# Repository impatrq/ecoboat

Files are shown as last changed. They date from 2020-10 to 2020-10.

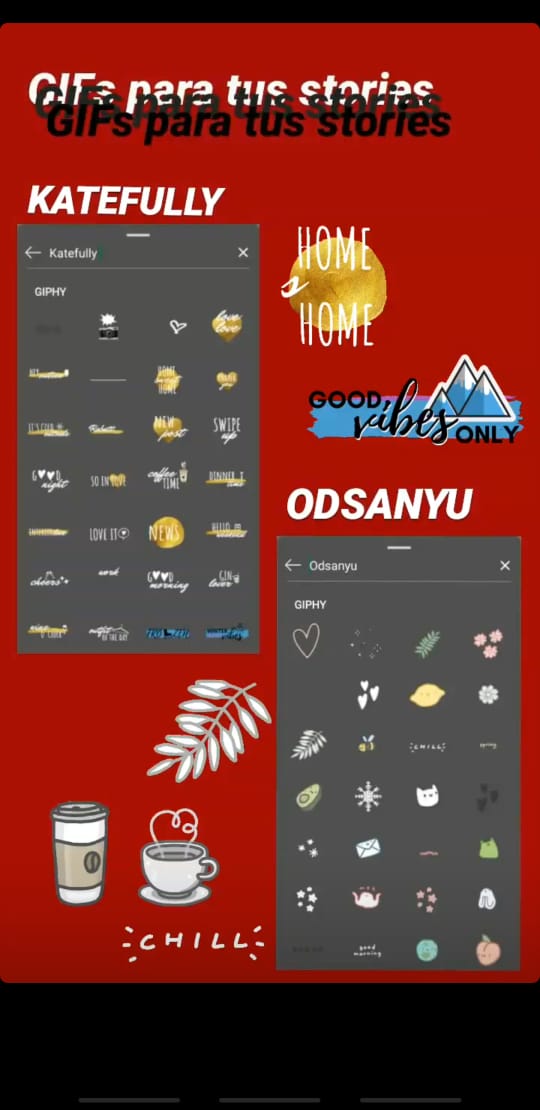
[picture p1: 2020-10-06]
Diseño/Instagram/WhatsApp Image 2020-04-10 at 20.14.38 (1).jpeg

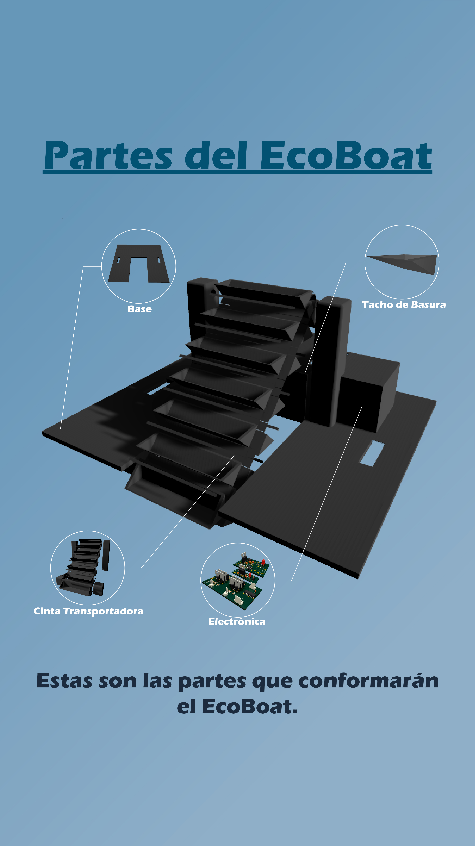
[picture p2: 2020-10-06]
Diseño/Instagram/Partes Historias-05.jpg

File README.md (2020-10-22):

# EcoBoat
Bienvenidos al repositorio de EcoBoat.

## Software

En la carpeta de "Software" se encontrarán con varios archivos:

- EcoBoat1.0: Es el código principal, donde se ejecuta el funcionamiento del barco y todas las librerías utilizadas para dicho fin.
- Motores: Es la librería (desarrollada por el equipo de EcoBoat) que se utiliza para controlar los motores.
- SensoresUS: Es la librería (desarrollada por el equipo de EcoBoat) que utilizamos para realizar las mediciones con los sensores Ultrasónicos.
- RedNeuronal: Es la librería (desarrollada por el equipo de EcoBoat) que contiene el código de la Red Neuronal y su entrenamiento.
- Módulo_Master: Es el programa utilizado para recibir la información y transferirla mediante sockets a la Interfaz de Usuario.
- Interfaz de Usuario: En esta carpeta se encuentran los códigos de la interfaz de usuario.
- Simulación: En esta carpeta encontrarán todo lo relacionado al entrenamiento de la Red Neuronal.
  - Aplicación Ejecutable: Aquí se encuentra la aplicación de la cual se obtienen los datos de entrenamiento para la red, es decir, la red aprende de las acciones realizadas en dicha aplicación.
  - Código fuente: Contiene el programa de la simulación.
  - trainData: En esta carpeta se guardan los archivos con la información de entrenamiento.

## Hardware

En esta carpeta se encuentran los diseños de todas las placas utilizadas:

- Circuito de Control de Marcha: Circuito utilizado para controlar los 3 motores del EcoBoat
- Fuente de 12V a 5V: regulador de tensión de 12 a 5V.
- Regulador de Carga: Es el circuito que controla la carga de la batería utilizando un panel solar.
- SensoresUS: Esta placa cumple la función de sincronizar la toma de datos de los sensores Ultrasónicos.
- Diagrama de Interconexión de circuitos: Es un diagrama que muestra como se conectan todas las placas del proyecto.

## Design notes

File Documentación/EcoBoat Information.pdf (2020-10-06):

Introduction:
EcoBoat is a school project whose objectives are to combat contamination by using a self-driving boat that collects floating residues from rivers and also to encourage people to take steps to prevent pollution.
Now we are working on a reduced-scale prototype. However, once this prototype is working, we intend to build this boat on a larger scale so that it can be used in rivers all around the world.

General Description:
EcoBoat will be at a charging station where it will charge by using solar energy, which will reduce contamination and will not generate any kind of residues. The station will be equipped with barriers to prevent the boat from being driven by the river's current.
Once the batteries are fully charged, the ship will set sail. This project will be provided with an autopilot which will controls every system of the EcoBoat; this way, there will be no need of a human to operate it. However, there will be a server which will have all the information needed to check whether the boat is working properly or not.
The user would have to introduce a route for the autopilot to follow. Once the boat is moving, it will catch the floating residues with the help of pitchers mounted in a conveyor belt and it will store them in a trash deposit in the back of the vehicle. When the route has all been covered, a person shall remove the deposit from the ship. It will go back to the charging station by its own means.

Technical Description:
EcoBoat will make use of a solar panel to charge its batteries. The user should establish a route for the boat to clean. This project will have a GPS in order to determine its location and a series of waypoints (in coordinates) will be established by an algorithm depending on the route previously introduced. This way, boat program will action its engine and its rudder in order to move it in the right direction. It will also be provided with ultrasonic sensors to prevent the ship from crashing with the borders of the river. Furthermore, it will have sounding lines to determine if the water level is enough to sail and to detect if there are any other ships nearby (in which case the boat will just stop).
Using pitchers, the boat will pick up the floating residues from the water and put them into a deposit. When EcoBoat finalizes its route, the trash will be removed manually and it will go back to the charging station.
This project will also have a real time diagnosis system of every part of the boat. This will be displayed in a comfortable graphic interface from a remote station.

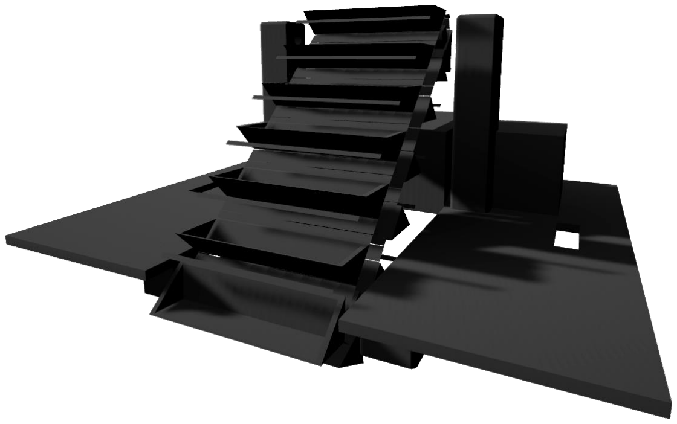
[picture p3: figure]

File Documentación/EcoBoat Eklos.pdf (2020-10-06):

# EcoBoat

Este proyecto consiste en un vehículo acuático diseñado para recolectar los desechos flotantes de ríos. Nuestro objetivo es reducir la contaminación de las aguas y concientizar sobre la contaminación causada por los residuos.

Actualmente estamos trabajando en un prototipo de tamaño reducido. No obstante, nuestro objetivo es que una vez que este sea funcional, podamos producir, este proyecto, en una escala más grande para poder recolectar mayor cantidad de basura. Este sistema podría ser utilizado por el Estado para mantener limpios todos los ríos de Argentina

Gracias a nuestro sistema de extracción de los elementos que se encuentran en la superficie de los ríos, podríamos no solo limpiar la superficie, sino también disminuir en gran medida la cantidad de basura que -de no ser extraída- empezaría a acumularse en el fondo del agua o llegaría al mar y el océano.

Además del gran impacto que este proyecto generaría en el medio ambiente, también buscamos concientizar a las personas sobre los residuos que arrojan al agua. Si trabajamos todos juntos, podemos reducir la contaminación de forma drástica

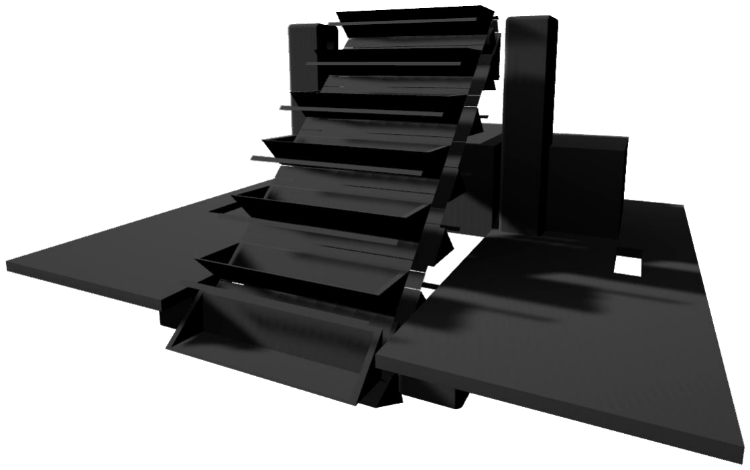
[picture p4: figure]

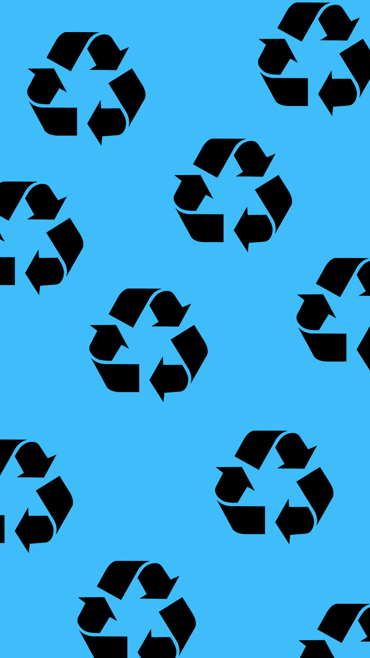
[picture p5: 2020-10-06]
Diseño/Instagram/Historias Trivia/reciclar.png

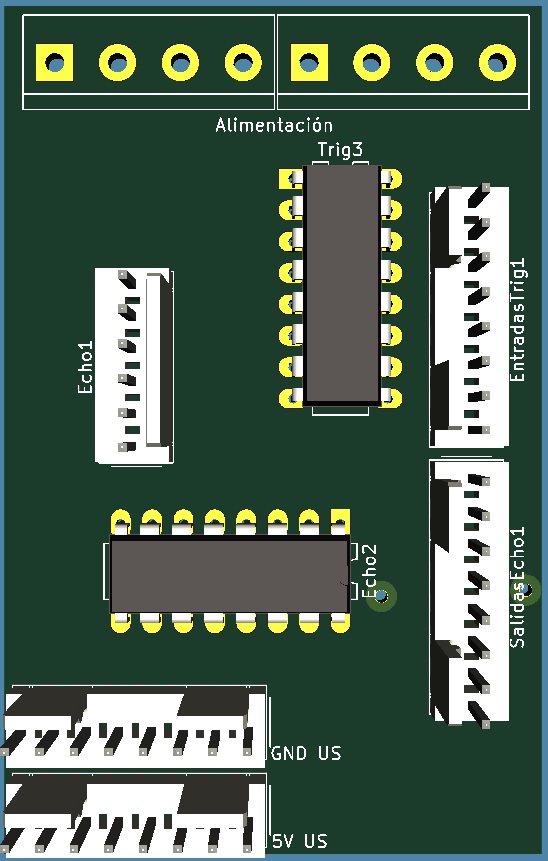
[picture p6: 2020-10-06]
Hardware/SensoresUS/3D SensoresUS.jpg

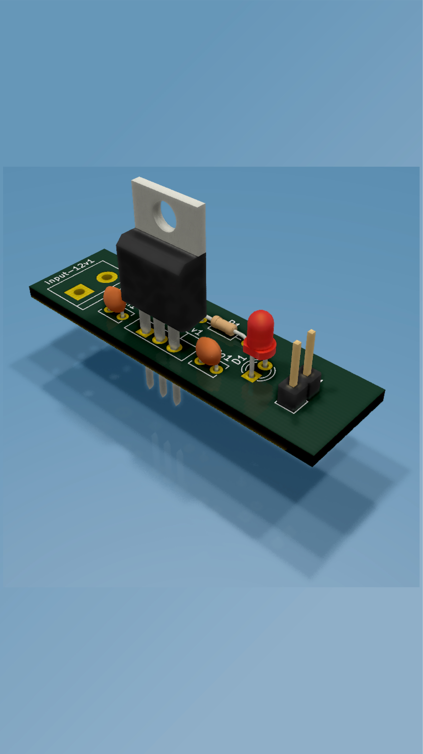
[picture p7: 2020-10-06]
Diseño/Instagram/Historia Circuito Regulador De Tensión-06-06-06.jpg

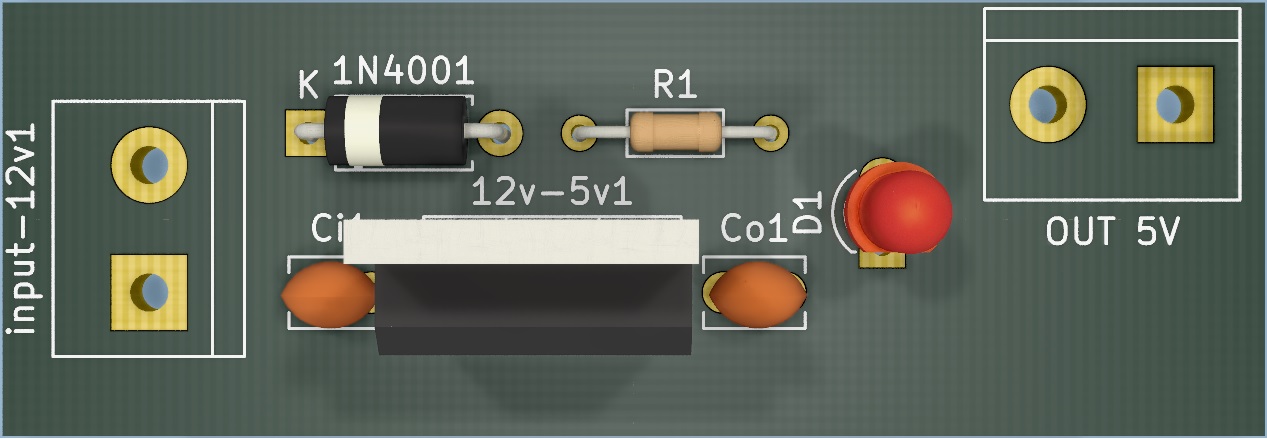
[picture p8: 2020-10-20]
Hardware/fuente 12v a 5v/Fuente 12V a 5V 3D.jpg

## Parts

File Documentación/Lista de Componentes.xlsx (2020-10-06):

Componente | Cantidad
Placa de Cobre 20x15 | 1
Cloruro Férrico | 1
FLUX aerosol | 1
Molex Macho 2 Pines | 2
Molex Hemra 2 Pines | 2
Molex Macho 3 Pines | 1
Molex Hembra 3 Pines | 1
Molex Macho 4 Pines | 2
Molex Hembra 4 Pines | 2
Molex Macho 6 Pines | 1 | Estos conectores no tienen que ser necesariamente molex
Molex Hembra 6 Pines | 1 | puede ser cualquier conector con 2,54mm de distancia entre
Molex Macho 7 Pines | 1 | pines y que tenga macho y hembra (con sus respectivos
Molex Hembra 7 Pines | 1 | conectores para cables)
Molex Macho 8 Pines | 4
Molex Hembra 8 Pines | 4
Conectores para Molex | 80 | (Terminales utilizados para conectar un cable a un molex hembra)
Pines Hembra a Macho | 40 | Tira de pines (2,54mm de separación entre pines) son para conectar a una raspberry
Termocontraible ø5mm | 80cm
Bornera 2 Polos | 11 | 126VP- 2P
Bornera 3 Polos | 2 | 126VP- 3P
MOSFET IRF9530 | 3
MOSFET IRF640 | 4
4N25 | 8
Resistencia 1,2K | 1
Resistencia 82K | 1
Preset 200K | 1 | Multivuelta
Preset 500K | 1 | Multivuelta
Diodo Zener 15V 1W | 1
Fusible 10A | 1
Capacitor 330nF | 3
Capacitor 100nF | 3
LM7805 | 2
LS157 | 1
MCP3008 | 1 | Conversor Analógico Digital con soporte para SPI
74HC237 | 1 | 3to8 dec
74LS151 | 1 | 8to1 mux
ACS712 ±20A | 2 | Sensor de Efecto HALL
Módulo RF NRF24 | 2 | Módulo de radio frecuencia

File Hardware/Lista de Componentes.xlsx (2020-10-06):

Componente | Cantidad
Placa de Cobre 20x15 | 1
Cloruro Férrico | 1
Molex Macho 2 Pines | 2
Molex Hemra 2 Pines | 2
Molex Macho 3 Pines | 1
Molex Hembra 3 Pines | 1
Molex Macho 4 Pines | 2
Molex Hembra 4 Pines | 2
Molex Macho 6 Pines | 1
Molex Hembra 6 Pines | 1
Molex Macho 7 Pines | 1
Molex Hembra 7 Pines | 1
Molex Macho 8 Pines | 4
Molex Hembra 8 Pines | 4
Conectores para Molex | 80 | (Terminales utilizados para conectar un cable a un molex hembra)
Pines Hembra a Macho | 40
Termocontraible | 80cm
Bornera 2 Pines | 8
Bornera 5 Pines | 1
Bornera 4 Pines | 2
MOSFET IRF9530 | 5
MOSFET IRF640 | 5
Transistores BJT | 8
Resistencia 220 | 8
Resistencia 1K | 1
Resistencia 1,2K | 1
Resistencia 10K | 8
Resistencia 82K | 1
Resistencia 270K | 1
Preset 200K | 1
Preset 500K | 1
Diodo | 1
Diodo Zener 15V | 1
Diodo LED | 2
Fusible 10A | 1
Capacitor 330nF | 3
Capacitor 100nF | 3
LM7805 | 2
Operacional | 1
UNL2003 | 1
MCP3008 | 1
74HC237 | 1
74LS151 | 1
ACS712 ±20A | 2
Módulo RF NRF24 | 2
Batería ciclo profundo | 1
Panel Solar | 1

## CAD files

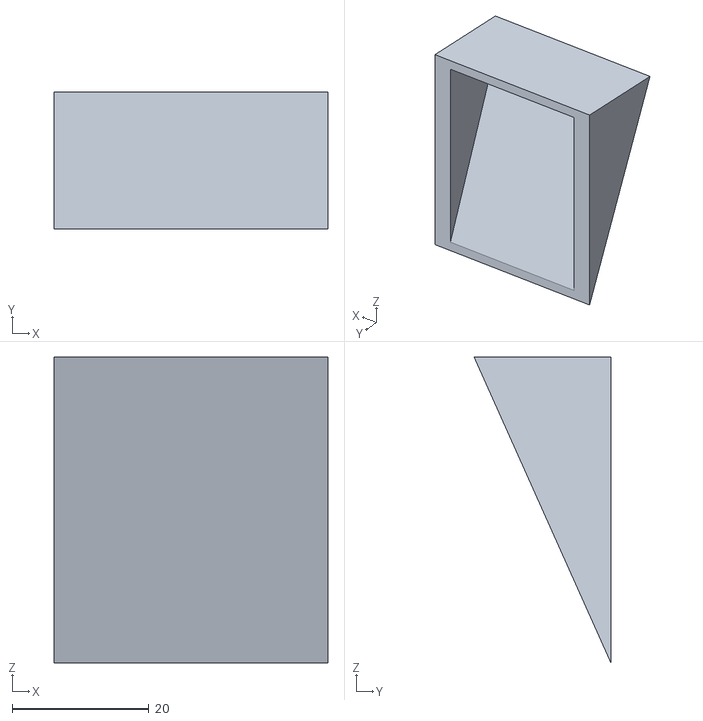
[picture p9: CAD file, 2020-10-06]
Estructura/Modelos 3D/Depósito de Basura.obj
40.0 x 20.0 x 44.7

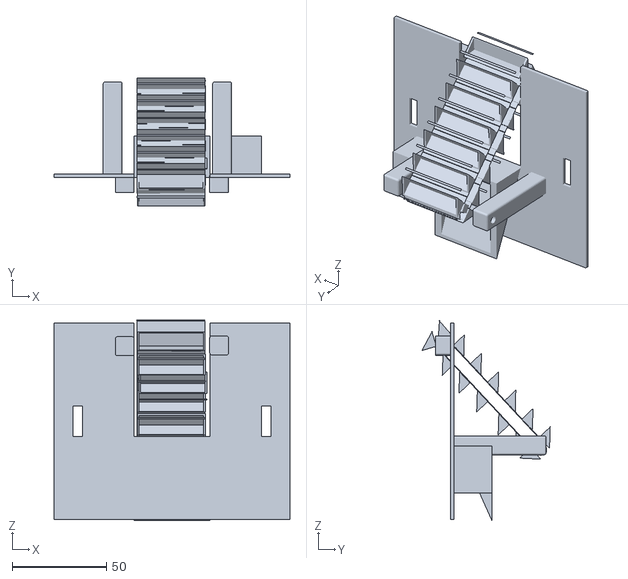
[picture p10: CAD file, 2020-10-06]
Estructura/Modelos 3D/diseño final.obj
125.0 x 68.0 x 106.2

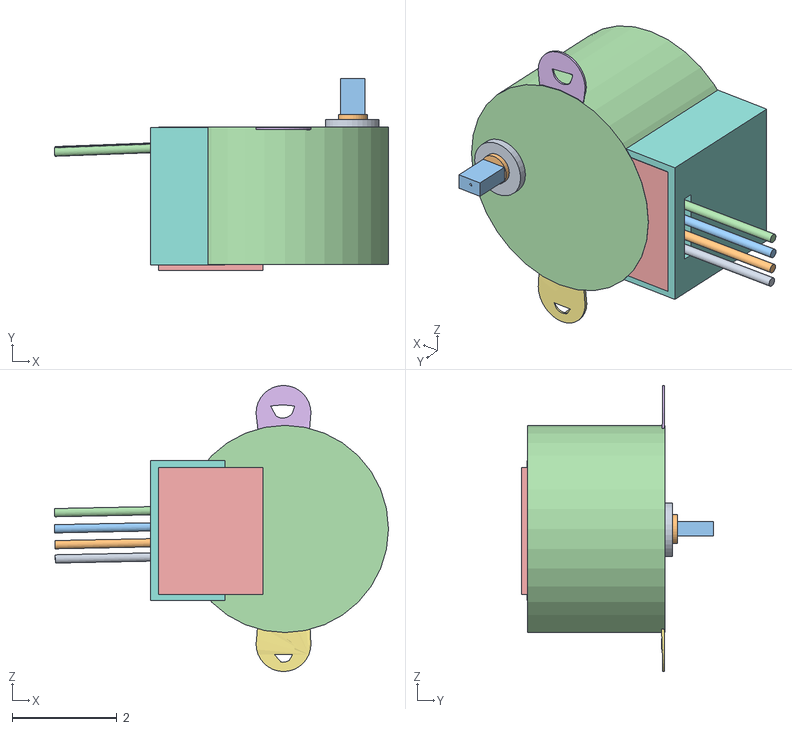
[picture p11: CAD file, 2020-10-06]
Estructura/Modelos 3D/Motor Paso a Paso.obj
6.39 x 3.68 x 5.47
Plane.025_Plane.006
Cylinder_Cylinder.003
Plane.026_Plane.007
Cylinder.003_Cylinder.004
Cylinder.004_Cylinder.005
Cube_Cube.001
Cylinder.005_Cylinder

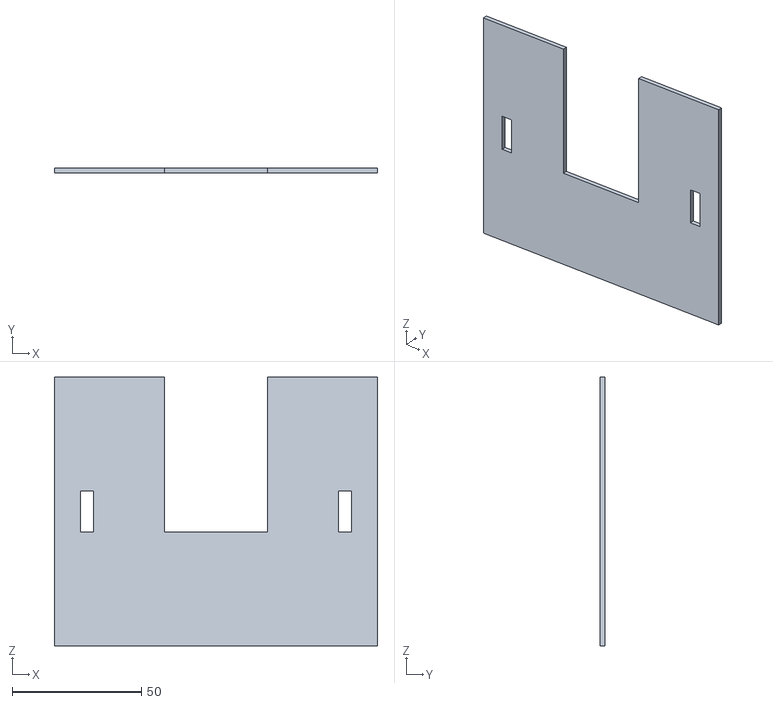
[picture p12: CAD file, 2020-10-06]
Estructura/Modelos 3D/Base.obj
125.0 x 2.00 x 104.1

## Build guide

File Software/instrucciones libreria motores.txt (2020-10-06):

paso a paso:

crear un objeto de la clase PaP con los 4 pines a usar como parametro: (pin1, pin2, pin3, pin4)
para girar en sentido horario usar la funcion girarH(grados)
para girar en sentido anti horario usar la funcion girarAH(grados)

motores lineales:

crear un objeto de la clase puenteH con los dos pines como parametro
el primer pin gira hacia la derecha y el segundo a la izquierda
funciones: para girar hacia la derecha: girarD()
	   para girar hacia la izquierda: girarI()
	   para frenar: detener()

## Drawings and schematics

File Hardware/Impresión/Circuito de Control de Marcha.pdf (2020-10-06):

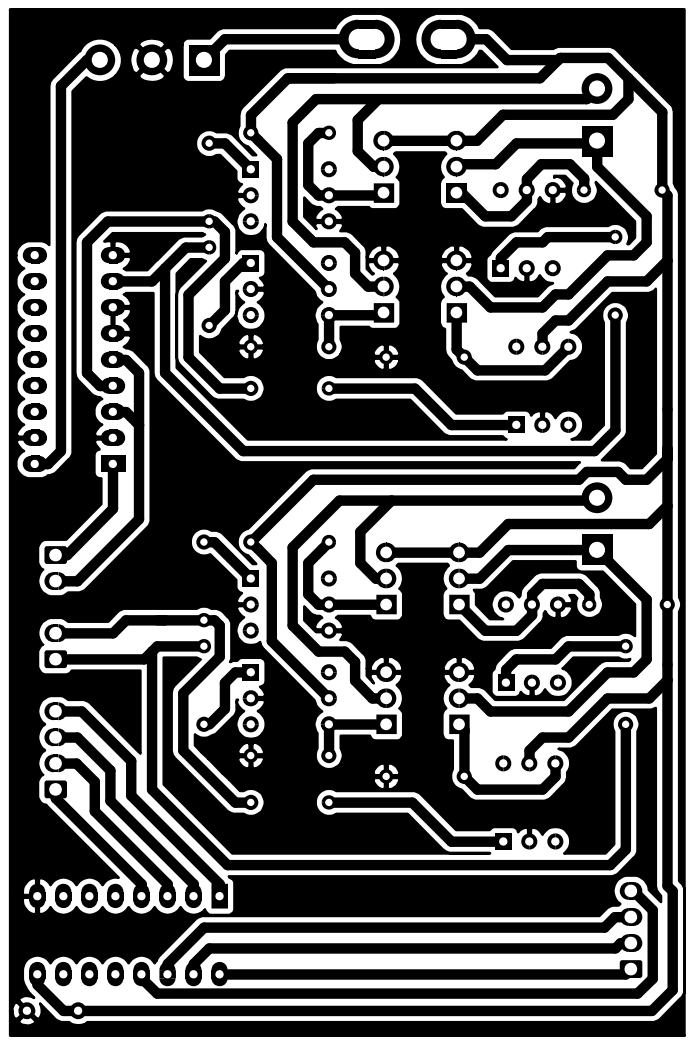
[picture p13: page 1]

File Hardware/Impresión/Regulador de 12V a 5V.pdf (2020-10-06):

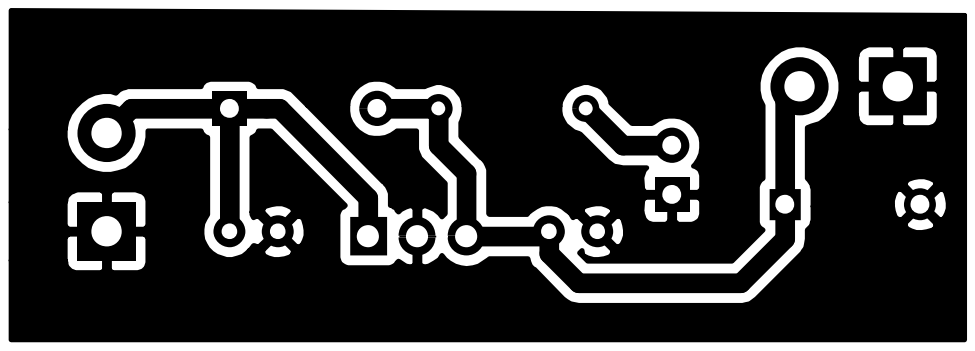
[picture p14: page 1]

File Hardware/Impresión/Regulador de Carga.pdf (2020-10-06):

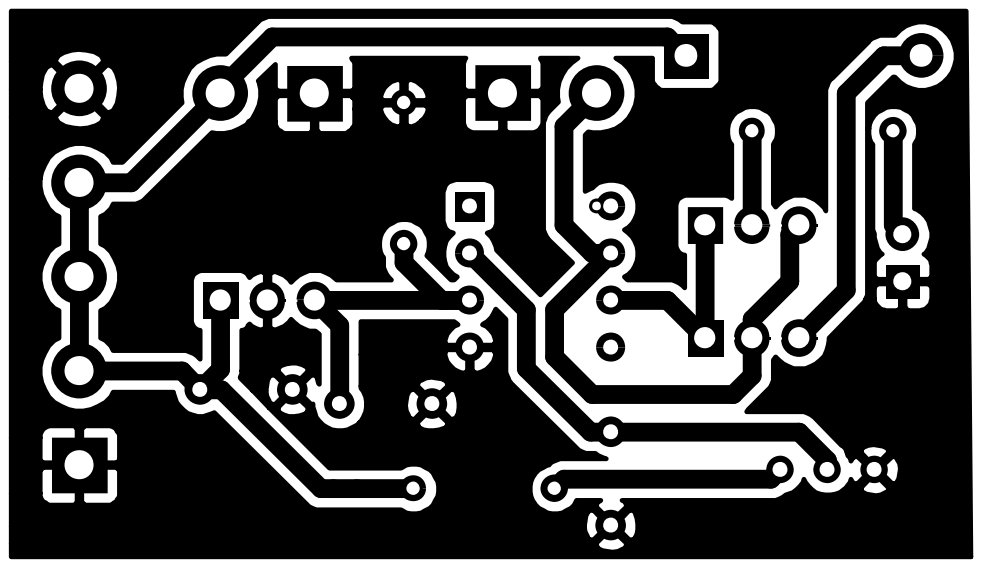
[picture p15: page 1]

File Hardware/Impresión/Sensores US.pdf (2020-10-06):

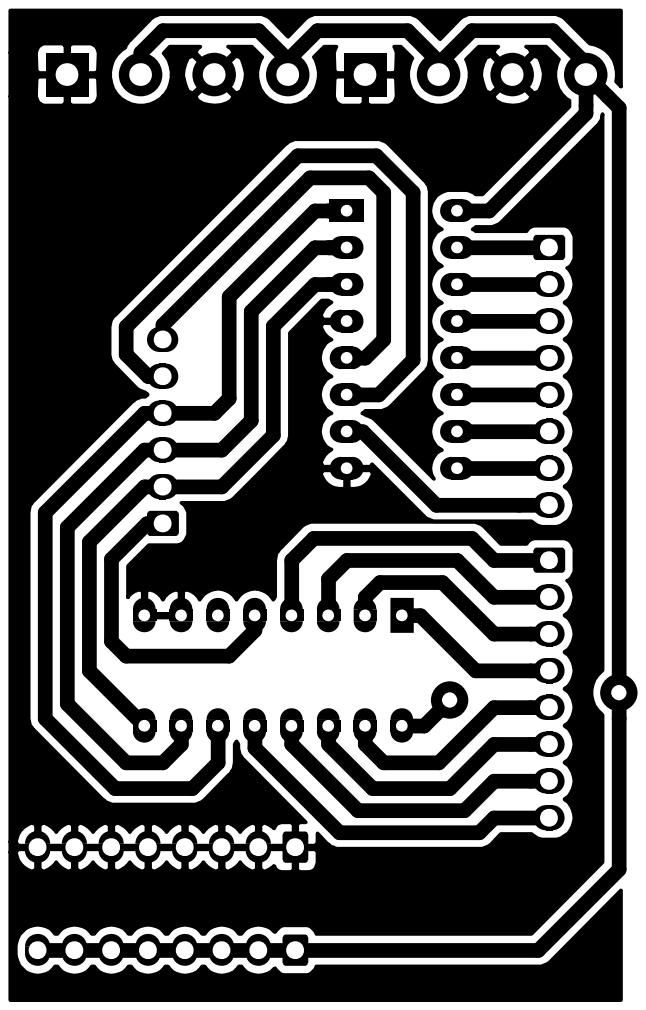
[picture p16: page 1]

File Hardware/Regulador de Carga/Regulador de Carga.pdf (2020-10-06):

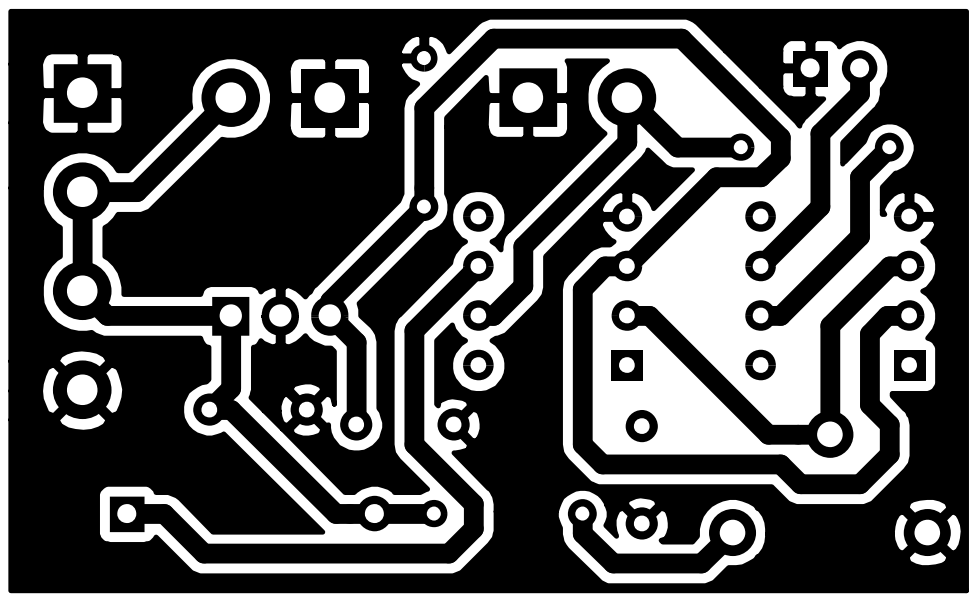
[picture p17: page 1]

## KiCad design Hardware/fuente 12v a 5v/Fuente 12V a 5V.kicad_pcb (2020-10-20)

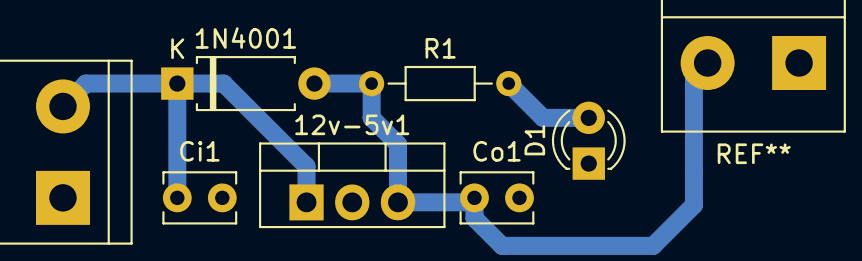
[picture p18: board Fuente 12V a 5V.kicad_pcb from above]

Board: 2 copper layers, 7 parts (0 on the bottom side), 4 nets.

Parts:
1N4001: D; D_A-405_P7.62mm_Horizontal
12v-5v1: LM7805_TO220; TO-220-3_Vertical
Ci1: 330n; C_Disc_D3.8mm_W2.6mm_P2.50mm
Co1: 100n; C_Disc_D3.8mm_W2.6mm_P2.50mm
D1: LED; LED_D3.0mm
R1: 1K; R_Axial_DIN0204_L3.6mm_D1.6mm_P7.62mm_Horizontal
input-12v1: 12v; TerminalBlock_bornier-2_P5.08mm

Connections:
GND: 12v-5v1.2, Ci1.2, Co1.2, D1.1, input-12v1.1
unnamed: 1N4001.1, 12v-5v1.1, Ci1.1, input-12v1.2
unnamed: 1N4001.2, 12v-5v1.3, Co1.1, R1.1
unnamed: D1.2, R1.2

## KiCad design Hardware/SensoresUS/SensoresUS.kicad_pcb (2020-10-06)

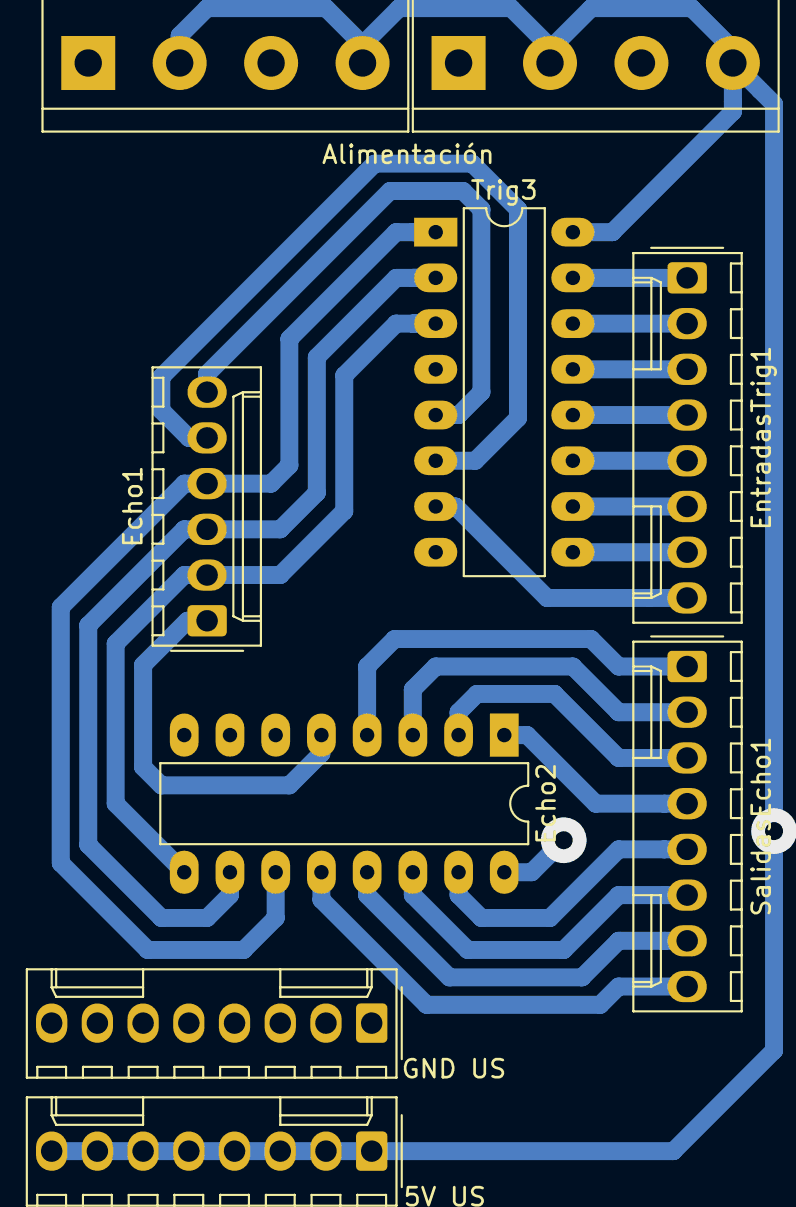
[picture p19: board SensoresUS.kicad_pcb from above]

Board: 2 copper layers, 8 parts (0 on the bottom side), 24 nets.

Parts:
5V US: Conn_01x08_Female; Molex_KK-254_AE-6410-08A_1x08_P2.54mm_Vertical
Alimentación: DOU; TerminalBlock_bornier-4_P5.08mm
Echo1: Conn_01x01_Female; Molex_KK-254_AE-6410-06A_1x06_P2.54mm_Vertical
Echo2: 74LS151; DIP-16_W7.62mm_LongPads
EntradasTrig1: Conn_01x08_Female; Molex_KK-254_AE-6410-08A_1x08_P2.54mm_Vertical
GND US: Conn_01x08_Female; Molex_KK-254_AE-6410-08A_1x08_P2.54mm_Vertical
SalidasEcho1: Conn_01x08_Female; Molex_KK-254_AE-6410-08A_1x08_P2.54mm_Vertical
Trig3: 74HC237; DIP-16_W7.62mm_LongPads

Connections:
5V: 5V US.1, 5V US.2, 5V US.3, 5V US.4, 5V US.5, 5V US.6, 5V US.7, 5V US.8, Alimentación.2, Alimentación.4, Echo2.16, Trig3.16
GND: Alimentación.1, Alimentación.3, Echo2.7, Echo2.8, GND US.1, GND US.2, GND US.3, GND US.4, GND US.5, GND US.6, GND US.7, GND US.8, Trig3.4, Trig3.8
unnamed: Echo1.1, Echo2.5
unnamed: Echo2.1, SalidasEcho1.4
unnamed: Echo2.2, SalidasEcho1.3
unnamed: Echo2.3, SalidasEcho1.2
unnamed: Echo2.4, SalidasEcho1.1
unnamed: Echo2.12, SalidasEcho1.8
unnamed: Echo2.13, SalidasEcho1.7
unnamed: Echo2.14, SalidasEcho1.6
unnamed: Echo2.15, SalidasEcho1.5
unnamed: EntradasTrig1.1, Trig3.15
unnamed: EntradasTrig1.2, Trig3.14
unnamed: EntradasTrig1.3, Trig3.13
unnamed: EntradasTrig1.4, Trig3.12
unnamed: EntradasTrig1.5, Trig3.11
unnamed: EntradasTrig1.6, Trig3.10
unnamed: EntradasTrig1.7, Trig3.9
unnamed: EntradasTrig1.8, Trig3.7
unnamed: Echo1.5, Trig3.6
unnamed: Echo1.6, Trig3.5
Select1: Echo1.4, Echo2.11, Trig3.1
Select2: Echo1.3, Echo2.10, Trig3.2
Select3: Echo1.2, Echo2.9, Trig3.3

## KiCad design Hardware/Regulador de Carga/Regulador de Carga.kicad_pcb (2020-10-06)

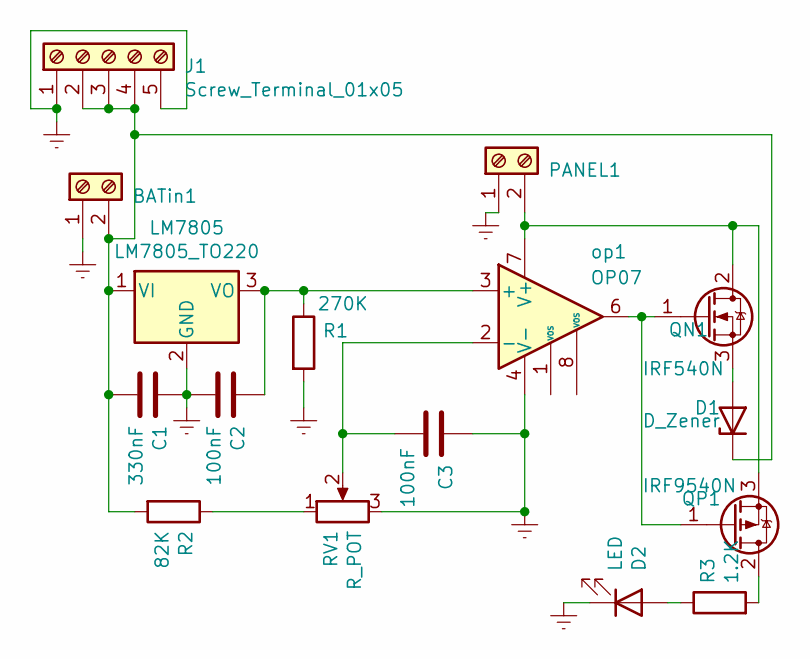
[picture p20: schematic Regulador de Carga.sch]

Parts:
BATin1: Screw_Terminal_01x02; TerminalBlock_bornier-2_P5.08mm
C1: 330nF; C_Disc_D4.3mm_W1.9mm_P5.00mm
C2, C3: 100nF; C_Disc_D4.3mm_W1.9mm_P5.00mm
D1: D_Zener; D_DO-15_P12.70mm_Horizontal
D2: LED; LED_D3.0mm
J1: Screw_Terminal_01x05; TerminalBlock_bornier-5_P5.08mm
LM7805: LM7805_TO220; TO-220-3_Vertical
PANEL1: Screw_Terminal_01x02; TerminalBlock_bornier-2_P5.08mm
QN1: IRF540N; TO-220-3_Vertical
QP1: IRF9540N; TO-220-3_Vertical
R1: 270K; R_Axial_DIN0204_L3.6mm_D1.6mm_P7.62mm_Horizontal
R2: 82K; R_Axial_DIN0204_L3.6mm_D1.6mm_P7.62mm_Horizontal
R3: 1.2K; R_Axial_DIN0204_L3.6mm_D1.6mm_P7.62mm_Horizontal
RV1: R_POT; Potentiometer_Bourns_3296W_Vertical
op1: OP07; DIP-8_W7.62mm

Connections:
Earth: BATin1.1, C1.1, C2.2, C3.1, D2.1 (K), J1.1, J1.5, LM7805.2 (GND), PANEL1.1, R1.2, RV1.3, op1.4 (V-)
unnamed: BATin1.2, C1.2, D1.1 (K), J1.2, J1.3, J1.4, LM7805.1 (VI), R2.2
unnamed: C2.1, LM7805.3 (VO), R1.1, op1.3 (+)
unnamed: C3.2, RV1.2, op1.2 (-)
unnamed: D1.2 (A), QN1.3 (S)
unnamed: D2.2 (A), R3.1
unnamed: PANEL1.2, QN1.2 (D), QP1.3 (S), op1.7 (V+)
unnamed: QN1.1 (G), QP1.1 (G), op1.6
unnamed: QP1.2 (D), R3.2
unnamed: R2.1, RV1.1

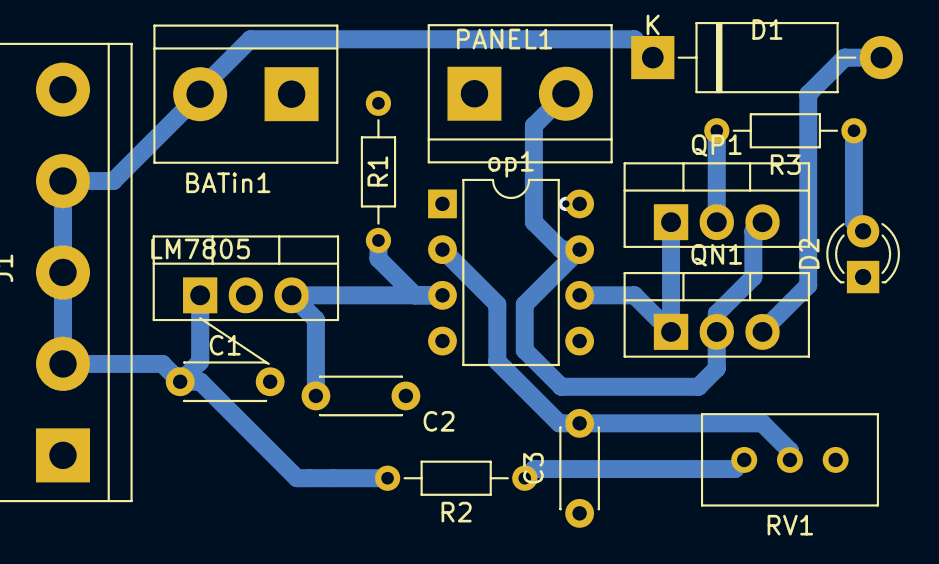
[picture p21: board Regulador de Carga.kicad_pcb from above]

Board: 2 copper layers, 16 parts (0 on the bottom side), 10 nets.

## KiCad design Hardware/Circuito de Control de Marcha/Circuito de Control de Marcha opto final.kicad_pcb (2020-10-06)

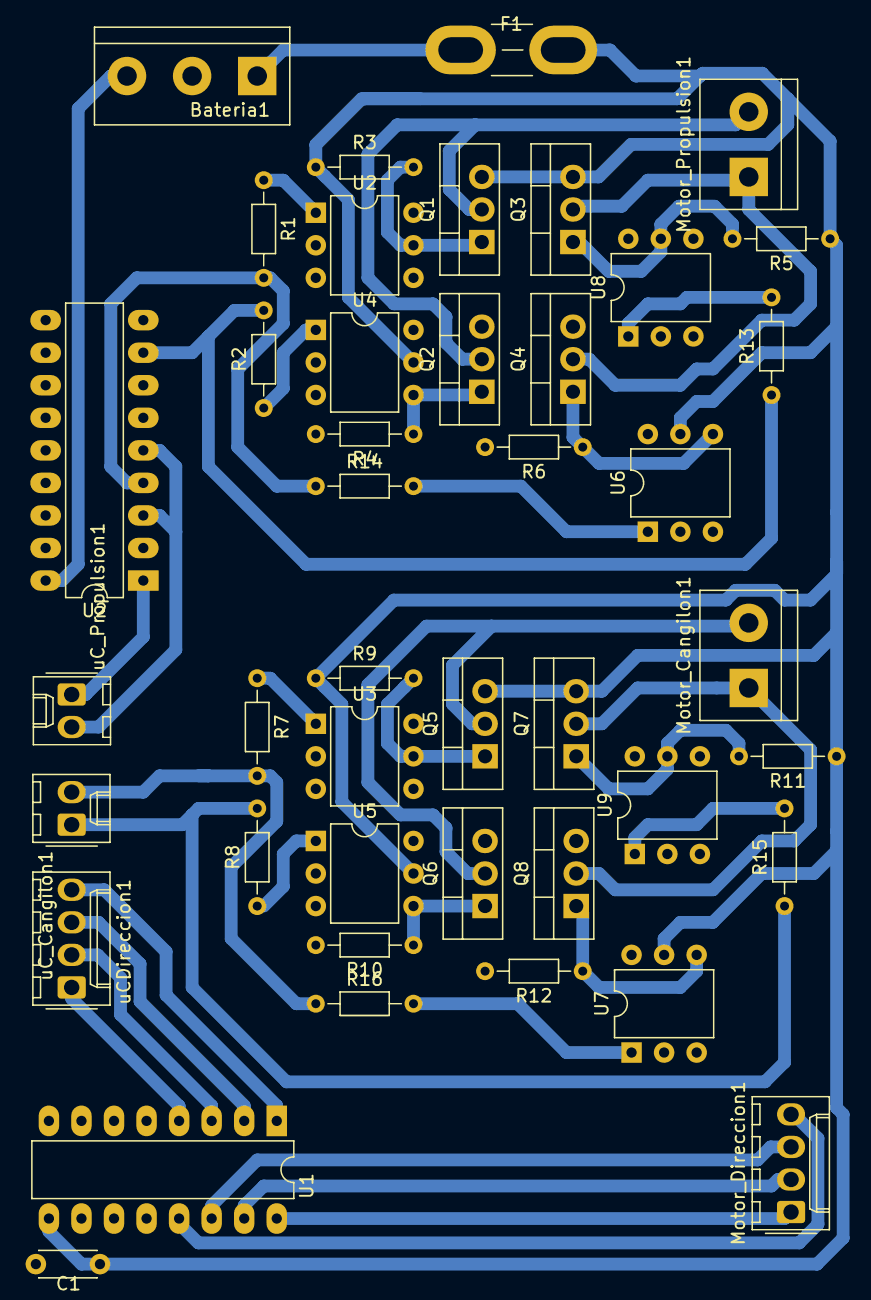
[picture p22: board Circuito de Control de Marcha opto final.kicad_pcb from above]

Board: 2 copper layers, 43 parts (0 on the bottom side), 37 nets.

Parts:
Bateria1: Screw_Terminal_01x02; TerminalBlock_bornier-3_P5.08mm
C1: C; C_Disc_D4.3mm_W1.9mm_P5.00mm
F1: Fuse; Fuse_Blade_Mini_directSolder
Motor_Cangilon1: Screw_Terminal_01x02; TerminalBlock_bornier-2_P5.08mm
Motor_Direccion1: Screw_Terminal_01x04; Molex_KK-254_AE-6410-04A_1x04_P2.54mm_Vertical
Motor_Propulsion1: Screw_Terminal_01x02; TerminalBlock_bornier-2_P5.08mm
Q1, Q3, Q5, Q7: IRF9540N; TO-220-3_Vertical
Q2, Q4, Q6, Q8: IRF540N; TO-220-3_Vertical
R1, R2, R7, R8, R13, R14, R15, R16: 220; R_Axial_DIN0204_L3.6mm_D1.6mm_P7.62mm_Horizontal
R3, R4, R5, R6, R9, R10, R11, R12: 10k; R_Axial_DIN0204_L3.6mm_D1.6mm_P7.62mm_Horizontal
U1: ULN2003; DIP-16_W7.62mm_LongPads
U2, U3, U4, U5, U6, U7, U8, U9: 4N25; DIP-6_W7.62mm
U2#2: 74LS157; DIP-18_W7.62mm_LongPads
uCDireccion1: Screw_Terminal_01x04; Molex_KK-254_AE-6410-04A_1x04_P2.54mm_Vertical
uC_Cangilon1: Screw_Terminal_01x02; Molex_KK-254_AE-6410-02A_1x02_P2.54mm_Vertical
uC_Propulsion1: Screw_Terminal_01x02; Molex_KK-254_AE-6410-02A_1x02_P2.54mm_Vertical

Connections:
Earth: Bateria1.2, C1.2, Q2.3, Q4.3, Q6.3, Q8.3, R4.2, R6.2, R10.2, R12.2, U1.8, U2.2, U2.4, U2#2.2, U2#2.6, U2#2.7, U2#2.9, U2#2.17, U3.2, U3.4, U4.2, U5.2, U6.2, U7.2, U8.2, U8.4, U9.2, U9.4
unnamed: Bateria1.1, F1.1
unnamed: C1.1, F1.2, Q1.3, Q3.3, Q5.3, Q7.3, R3.1, R5.1, R9.1, R11.1, U1.9, U4.5, U5.5, U6.5, U7.5
unnamed: Motor_Cangilon1.1, Q7.2, Q8.2
unnamed: Motor_Cangilon1.2, Q5.2, Q6.2
unnamed: Motor_Direccion1.1, U1.16
unnamed: Motor_Direccion1.2, U1.15
unnamed: Motor_Direccion1.3, U1.14
unnamed: Motor_Direccion1.4, U1.13
unnamed: Motor_Propulsion1.1, Q3.2, Q4.2
unnamed: Motor_Propulsion1.2, Q1.2, Q2.2
unnamed: Q1.1, R3.2, U2.5
unnamed: Q2.1, R4.1, U4.4
unnamed: Q3.1, R5.2, U8.5
unnamed: Q4.1, R6.1, U6.4
unnamed: Q5.1, R9.2, U3.5
unnamed: Q6.1, R10.1, U5.4
unnamed: Q7.1, R11.2, U9.5
unnamed: Q8.1, R12.1, U7.4
unnamed: R1.1, U2.1
unnamed: R1.2, R14.1, U2#2.4
unnamed: R2.1, U4.1
unnamed: R7.1, U3.1
unnamed: R8.1, U5.1
unnamed: R2.2, R13.1, U2#2.8
unnamed: R13.2, U8.1
unnamed: R14.2, U6.1
unnamed: R8.2, R15.1, uC_Cangilon1.1
unnamed: R15.2, U9.1
unnamed: R7.2, R16.1, uC_Cangilon1.2
unnamed: R16.2, U7.1
unnamed: U1.1, uCDireccion1.4
unnamed: U1.2, uCDireccion1.3
unnamed: U1.3, uCDireccion1.2
unnamed: U1.4, uCDireccion1.1
unnamed: U2#2.1, uC_Propulsion1.1
unnamed: U2.3, U2#2.3, U2#2.5, uC_Propulsion1.2

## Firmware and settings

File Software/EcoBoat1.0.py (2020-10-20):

import RPi.GPIO as GPIO			#Libreréa de pines GPIO
import time
import threading 				#Librería de los hilos
import pynmea2 as nmea 			#Librería del GPS
import serial 					#Librería para el puerto serial del GPS
import numpy as np 				#Librería de arrays
import motores as mt 			#Librería de los motores (Desarrollada por el equipo de EcoBoat)
import math 					#Librería de funciones matemáticas
from lib_nrf24 import NRF24 	#Librería del NRF24l01
import spidev 					#Librería de comunicación SPI
import sensoresUS as US 		#Librería de los Sensores Ultrasónicos (Desarrollada por el equipo de EcoBoat)
from RedNeuronal import *       #Librería de la Red Neuronal (Desarrollada por el equipo de EcoBoat)

#Defino el modo de uso de los pines GPIO
GPIO.setmode(GPIO.BCM)

#---------------------Variable global-----------------------
class Data():	#Aca guardamos todos los datos que van a ser utilizados por más de un hilo

	def __init__(self):
		self.lat=0		#Latitud
		self.long=0		#Longitud
		self.curso=0	#Curso
		self.escan=0	#Esta variable sirve para saber si el GPS recibe datos
		self.fin=0		#Esta variable es para detectar cuando el barco finaliza su recorrio
		self.timon=0	#Ángulo del timón, se utiliza para controlar el motor paso a paso
		self.bateria=0  #Porcentaje de batería
		self.motProp=0  #Consumo del motor de propulsión
		self.motCang=0  #Consumo del motor de la cinta transportadora

DATOS= Data()
#-----------------------------------------------------------

#--------------------------------------------------------------------GPS-----------------------------------------------------------------------
def GPS():

	def disponible():
		while True:
	        #Función que detecta disponibilidad de datos
	        port="/dev/ttyAMA0"		#Puerto UART de la Raspberry
			ser=serial.Serial(port, baudrate=9600, timeout=0.5)	#Inicio el puerto serial
			#Mido posición con el GPS
			dataout=pynmea2.NMEAStreamReader()
			data=ser.readline()
			#Tomo únicamente la línea que nos interesa que posee la posición
	        if data[0:6] == b'$GPRMC':
			    data = data.decode("utf-8","ignore")
			    datos=pynmea2.parse(data)
			    DATOS.lat = datos.latitude
			    DATOS.long = datos.longitude
			    DATOS.curso = datos.true_course

			    DATOS.escan = 1
			    break
        return 0
        
	def lectura(self):	#----------------Función que toma los datos de posición-------------------
		port="/dev/ttyAMA0"		#Puerto UART de la Raspberry
		ser=serial.Serial(port, baudrate=9600, timeout=0.5)	#Inicio el puerto serial
		
		while True:
			#Mido posición con el GPS
			dataout=pynmea2.NMEAStreamReader()
			data=ser.readline()

			#Tomo únicamente la línea que nos interesa que posee la posición
			if data[0:6] == b'$GPRMC':
			    data = data.decode("utf-8","ignore")
			    datos=pynmea2.parse(data)
			    DATOS.lat = datos.latitude
			    DATOS.long = datos.longitude
			    DATOS.curso = datos.true_course

			#Si el barco finalizó el recorrido, salimos del while
			if DATOS.fin = 1:
				break


	while DATOS.escan != 1:
		disponible()	#Una vez que detecto disponibilidad de datos inicio la lectura de datos e inicio los otros
						#hilos

    lectura()                
#-------------------------------------------------------------------------------------------------------------------------------------------

#--------------------------------------------------------Conversor Analógico/Digital--------------------------------------------------------
def conversor():	#El conversor A/D funciona con comunicación SPI
	#Inicio la comunicación SPI
	spi = spidev.SpiDev()
	spi.open(0, 0)

	spi.max_speed_hz = 300000
	spi.mode = 0

	while True:
		for canal in range (0, 3):	#Voy tomando los datos de todos los canales
			#Primero tomamos los datos crudos del conversor A/D (le digo que canal y que modo quiero usar)
	        datosCrudos = spi.xfer([(12 + canal), 0, 0])
	        #Proceso esta información para tenerla en un numero de 0 a 255
	        datosProcesados = ((datosCrudos[1]) << 1) + (datosCrudos[2] >> 7)

	        #--------------------------------------------Conversión a porcentaje de batería--------------------------------------------
	        if canal == 0:	#Canal del sensor de porcentaje de la batería
			    if datosProcesados < 201: #Si es menor a 201 bits significa que estoy al 0% (11,8V)
			    	porcentaje = 0
			    else:
			    	#Si el valor es igual o mayor a 201 calculo el procentaje
			    	porcentaje = ((datosProcesados - 201) * 100) / float(255 - 201) 
			    	porcentaje = round(porcentaje)
			    
			    DATOS.bateria = porcentaje 	#Guardo el valor en la variable global

			#-----------------------------------------------Conversión a grados del timón----------------------------------------------
			elif canal == 1:	#Canal del sensor de posición del timón
				#La marca de 0 grados está justo en el medio del pote, por ende, es una conversión de sumar.
	        	grados = -128 + datosProcesados		
	        	
	        	DATOS.timon = grados 	#Guardo el valor en la variable global

	        #------------------------------------------Conversión a consumo de los motores (A)-----------------------------------------
	        elif canal == 2 or canal == 3:	
	        	voltaje = (datosProcesados * 5) / float(255) #Convierto el valor en bits a volts (0 a 5V)
			    voltaje = round(voltaje, 3) #Redondeo a tres decimales
			    if voltaje <= 2,5: #Si es negativo
			    	consumo = - (voltaje * 0.1) #Convierto el valor de voltaje en corriente (Relación: 100mV = 1A)

			    else: #Si es positivo
			    	consumo = (voltaje - 2.5) * 0.1 #Convierto el valor de voltaje en corriente (Relación: 100mV = 1A)

			   	if canal == 2: #Canal del sensor de corriente del motor de propulsión
				    DATOS.motProp = consumo 	#Guardo el valor en la variable global
				   	
				elif canal == 3: #Canal del sensor de corriente del motor de la cinta Transportadora
					DATOS.motCang = consumo  	#Guardo el valor en la variable global

			#Cuando se finaliza el recorrido, dejamos de sensar datos.
			if DATOS.fin == 1:
				spi.close()
				break
#-------------------------------------------------------------------------------------------------------------------------------------------

#-------------------------------------------------------------Piloto automático-------------------------------------------------------------
def pilotoAutomático():
	#---------------------------------------------Funciones de navegación---------------------------------------------
	#Esta función se utilzia para medir la distancia entre la ubicación actual y el próximo waypoint
	def distancia(lat1, lng1 , waypoint):	#lat1 y lng1 son los datos de posición actual
		lat2=waypoint[0, 0]
		lng2=waypoint[0, 1]
		r=6371000
		c=(math.pi)/180
		#Fórmula de haversine
		a = sin(c*(lat2-lat1)/2)**2
		b = cos(c*lat1)*cos(c*lat2)*sin(c*(long2-long1)/2)**2
		d = 2*r*asin(sqrt(a + b))
		return d

	#Esta función nos otorga el curso deseado
	def DireccionDeseada(lat1, lng1, waypoint):
		lat2=waypoint[0, 0]
		lng2=waypoint[0, 1]
		dlon=lng2-lng1 
		a1=sin(dlon)*cos(lat2)
		a2=(cos(lat1)*sin(lat2))-(sin(lat1)*cos(lat2)*cos(dlon))
		curso=atan2(a1, a2)

		if(curso < 0):
			curso += 2*math.pi

		return degrees(curso)

	#Est afunción nos indica cuando llegamos al waypoint
	def LlegadaAlWP(destino):
		#comparar nuestra direccion con el destino
		dis= distancia(DATOS.lat, DATOS.long, destino)

		if(abs(dis) <= 2):	#Detectamos que llegamos al wp una vez que estamos a menos de 2 metros (por los errores del GPS)
			return 0
		else:
			return 1
	#------------------------------------------------------------------------------------------------------------------

	#--------------------------------------------------Red Neuronal----------------------------------------------------
	def redNeuronal(curso, waypoint): 
	#Esta función se utiliza para detectar si hay algún obstáculo. En caso de haberlo, iniciamos la RedNeuronal para esquivar.
		#curso= 0 yendo hacia adelante
		#curso=-2 yendo a izquierda
		#curso= 1 yendo a derecha 
		med=US.lectura()
		entradas= np.empty((1, 10))

		for i in range(10):
			entradas[i]=med[i]

		while med[3]<400 or med[4]<400 or (curso!=0 and med[4+curso]<400): 
			entradas[8]=DATOS.curso
			entradas[9]=DireccionDeseada(DATOS.lat, DATOS.long, waypoint)
					
			angulo=RN.resultado(entradas)
			if angulo > 0:	#Si el giro es positivo
	        	while DATOS.timon != angulo:	#Giro hasta que el sensor del timón detecte que se lelgo al valor deseado
	        		timon.girarAH()
	        if angulo < 0:	#Si el giro es negativo
	        	while DATOS.timon != angulo:	#Giro hasta que el sensor del timón detecte que se lelgo al valor deseado
	        		timon.girarH()

	        med=US.lectura()
			entradas= np.empty((1, 10))
			for i in range(10):
				entradas[i]=med[i]	

	#------------------------------------------------------------------------------------------------------------------

	#---------------------------------------------------Control PID----------------------------------------------------
	def controlPID(waypoint):	#Es el algoritmo que controla el giro del timón
		KP = 1 #Constante Proporcional
	    KI = 0.1 #Constante Integral
	    KD = 0.2 #Constante Derivativa
	    ZI = 5 #Zona activa de la Integral
	        
	    DD= DireccionDeseada(DATOS.lat, DATOS.long, waypoint)
	    DA= DATOS.curso #Direccion actual dado por el modulo gps
	    DeltaD= DD - DA 	#Con estos 3 renglones tomamos la diferencia entre el curso actual y el deseado

	    errorT = 0	#Variable para cuando se activa la zona integral
	    
	    while DeltaD >= 0.05 or DeltaD <= -0.05: #Le pusimos que funcione hasta un error un poco mayor a 0 debido a el margen de error del GPS
	        #Si el GPS no encuentra un Curso salgo del PID
	        if DATOS.curso == None:
	        	break

	        #Primero calculo el error	
	        DD= DireccionDeseada(DATOS.lat, DATOS.long, waypoint)
	        DA= DATOS.curso #Direccion actual dado por el modulo gps
	        DeltaD= DD - DA
	            
	        if DeltaD <= ZI and (DeltaD >= 0.005 or DeltaD <= -0.005):
	            #Si estamos en la zona activa de la integral empezamos a sumar ángulo
	            errorT += DeltaD
	        else:
	            #Si estamos fuera de la zona activa de la integral, asignamos un 0 a la integral
	            errorT = 0

	        if errorT >= 50/KI:
	            #Le ponemos un límite a la integral
	            errorT = 50/KI
	            
	        UltimoError = DeltaD #Guardo el último error
	        Proporcional = DeltaD * KP
	        Integral = errorT * KI
	        Derivativa = (DeltaD - UltimoError) * KD

	        #Obtengo el valor del ángulo para el timón
	        angulo = Proporcional + Integral + Derivativa

	        if abs(angulo) >= 30:
	            #Si el ángulo es mayor que el máximo de giro del timón giro 30°
	            angulo = (DeltaD/ abs(DeltaD))*30 #el angulo toma el signo del DeltaD

	        if angulo < 0:	#Si el giro es negativo
	        	while DATOS.timon != angulo:	#Giro hasta que el sensor del timón detecte que se llego al valor deseado
	        		redNeuronal(-2, waypoint)	#Corro el esta funcion por si hay obstáculos mientras giro
	        		timon.girarH()	#Giro Horario

	        if angulo > 0:	#Si el giro es positivo
	        	while DATOS.timon != angulo:	#Giro hasta que el sensor del timón detecte que se llego al valor deseado
	        		redNeuronal(1, waypoint)	#Corro el esta funcion por si hay obstáculos mientras giro
	        		timon.girarAH()	#Giro AniHorario

	        return angulo
	#------------------------------------------------------------------------------------------------------------------

	#--------------------------------------------Inicio el piloto automático-------------------------------------------
	#Creo objetos para los motores
	timon= mt.PaP(4, 17, 27, 22)
	Cangilon= mt.Cangilon(6, 13, 100)			#Con un 1 en el pin de selección giramos horario, con un 0 antihorario.
	motorDirec= mt.Propulsion(18, 12, 100)		#Con el 12 giro horario y con el 18 antihorario.

	#Comienzo a girar los motores de propulsión y de la cinta trtansportadora
	Cangilon.girarD()
	motorDirec.girarD()

	#inicio la red neuronal
	#hay que cargar un archivo que tenga la red ya entrenada
	RN= RedNeuronal()

	#En esta array se guardan los waypoints a recorrer 
	#Cada waypoint se guarda en una fila distinta
	waypoints= np.array(([lat1, lng1], [lat2, lng2], ..., [latn, lngn]))

	#Se recorren todos los watpoints uno por uno
	for i in range (0, len(waypoints)):
		#La idea es que corrija el rumbo a lo largo del trayecto
		while(LlegadaAlWP(waypoints[i]) != 1):
			redNeuronal(0, waypoints[i])	#Detecto si hay obstáculos

			if DATOS.curso != None:		#Solo corrijo el rumbo si hay un curso detectado
				controlPID(waypoints[i])	#Si el curso no es el deseado se activará el PID

	#Detengo los motores de propulsión y la cinta transportadora
	Cangilon.detener()
	motorDirec.detener()

	DATOS.fin = 1	#Indico que finalizó el recorrido
#-------------------------------------------------------------------------------------------------------------------------------------------

#--------------------------------------------------------------Módulos RF-------------------------------------------------------------------
def módulosRF():
	#-----------------------------Funciones de enviar y recibir-----------------------------
	def enviar(dato):
	    datoStr = str(dato) #Convierto el dato en string
	    datoSend = list(datoStr) #Lo separo en letras
	    radio.Write(datoSend) #Lo envio

	def recibir():
	    #Guardo el mensjae en una variable
	    msjRecibido = []
	    radio.read(msjRecibido, radio.getDynamicPayloadSize())

	    #Decodifico el mensaje
	    mensaje = ""
	    for n in msjRecibido
	        if (n >= 32 and n <= 126)
	            mensaje += chr(n)
	    return mensaje
	#----------------------------------------------------------------------------------------

	#-------------------------------Configuración del NRF24l01-------------------------------
	#Estas son las direcciones que les asignamos a las direcciones de lectura y escritura
	pipes = [[0xe7, 0xe7, 0xe7, 0xe7, 0xe7], [0xc2, 0xc2, 0xc2, 0xc2, 0xc2]]

	radio = NRF24(GPIO, spidev.SpiDev())	#Creamos el objeto de la radio

    radio.begin(0, 7)	#Iniciamos la radio

    radio.setRetries(15,15)		#Cantidad de intentos
    radio.setPayloadSize(32)	#Tamaño máximo de los mensajes
    radio.setChannel(0x60)		#Canal de comunicación
    radio.setDataRate(NRF24.BR_2MBPS)	#Velocidad de transferencia
    radio.setPALevel(NRF24.PA_MAX)		#Consumo del módulo, esto define el alcance

    #Estas funcioines sirven para que el módulo sepa si se recibió el mensaje que envió
    radio.setAutoAck(True)
    radio.enableDynamicPayloads()
    radio.enableAckPayload()

    #Abro las direcciones
    radio.openReadingPipe(1, pipes[1])
    radio.openWritingPipe(pipes[0])

    radio.startListening()
    #-----------------------------------------------------------------------------------------

    #Se queda esperando un mensaje
    while not radio.available(0):
        time.sleep(1/100)

    #Cuando detecta un mensaje, lo guardo en una variable
    comando = recibir()

	#-----------------------------------Comando: ZARPAR---------------------------------------
	if comando == MSJZARPAR:	#Cuando recibo la orden de zarapar tengo que inicar los otros hilos
		TGPS = threading.Thread(name="GPS", target=GPS)		#Creo el hilo del GPS
		TPA = threading.Thread(name="PA", target=pilotoAutomatico)	#Creo el hilo del piloto automático
		TCAD = threading.Thread(name="CAD", target=conversor)	#Creo el hilo del Conversor A/D
		#Inicio el GPS
		TGPS.start()
		
		while True:		#Espero a que el GPS reciba datos
    		if(DATOS.escan==1):
        		break
		#Inicio el Piloto Automático y el conversor A/D
		TCAD.start()
		TPA.start()

		#Envió información a la interfaz de usuario
		while True:
			enviarRF(DATOS.lat)		#Latitud
			enviarRF(DATOS.lon)		#Longitud
			enviarRF(DATOS.curso)	#Curso
			enviarRF(DATOS.motProp)	#Consumo del motor de Propulsión
			enviarRF(DATOS.motCang)	#Consumo del motor de la Cinta Transportadora
			enviarRF(DATOS.bateria)	#Porcentaje de Batería
			enviarRF(DATOS.timon)	#Grados del Timón
			#Si el barco finalizó el recorrido, dejo de enviar datos
			if DATOS.fin == 1:
				break
	#---------------------------------------------------------------------------------------
#-------------------------------------------------------------------------------------------------------------------------------------------

#-----------------------------------------------------------Inicio el programa--------------------------------------------------------------
#Creo el hilo del módulo RF
TRF = threading.Thread(name="RF", target=comRF)

#Inicio un bucle para que cuando el programa finalice, siga esperando a recibir orden de salir de vuelta.
while True:
	TRF.start()

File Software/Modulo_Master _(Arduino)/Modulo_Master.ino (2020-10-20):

#include<SPI.h>
#include<RF24.h>

//ce, csn pins
RF24 radio(9, 10);

void setup(void) {
//-------------------------------------------------------------------------Configuración del Módulo Master------------------------------------------------------------------------
  radio.begin();  
  radio.setPALevel(RF24_PA_MAX);  //Definimos la potencia del módulo
  radio.setChannel(0x76); //Canal
  radio.openWritingPipe(0xF0F0F0E1LL);  //Direcciones de escritura y lectura
  const uint64_t pipe = 0xE8E8F0F0E1LL;
  radio.openReadingPipe(1, pipe);

  radio.enableDynamicPayloads();
  radio.powerUp();  //Iniciamos la radio
}

//------------------------------------------------------------------------------------------------------------------------------------------------------------------------------

//---------------------------------------------------------------------Funciones de enviar y recibir mensajes-------------------------------------------------------------------
int enviarRF(int msj){
  //Convierto el mensaje en un string
  String msjStr(msj);
  const char texto[] = "msjStr";
  //Lo envío
  return msj;
}

String recibirRF(){
  char msjRecibido[32] = {0};
  //Leo el mensaje y lo guardo en una variable
  radio.read(msjRecibido, sizeof(msjRecibido));
  //Lo decodifico a un string
  String mensaje(msjRecibido);
  return mensaje;
}
//------------------------------------------------------------------------------------------------------------------------------------------------------------------------------

void loop(void) {
  char MSJZARPAR = "!ZARPAR";
  char comando;
  comando = enviarRF(MSJZARPAR);
  radio.write(comando, sizeof(comando));  //Envio el comando

  radio.startListening();   //Empiezo a escuchar

  //---------------------Comando Zarpar------------------------------
  if (comando == MSJZARPAR){
    if (radio.available()){
      while (true){
        String mensaje;
        latitud = recibirRF();
        longitud = recibirRF();
        curso = recibirRF();
        consProp = recibirRF();
        consCang = recibirRF();
        bateria = recibirRF();
        timon = recibirRF();
        }
        delay(500);
      }
   }
  }
  //-----------------------------------------------------------------
}

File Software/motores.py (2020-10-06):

import RPi.GPIO as gpio 
import time 
import numpy as np 

#agregar configuracion de pines gpio

estados=np.array([
    ["True","False","False","False"],
    ["False","True","False","False"],
    ["False","False","True","False"],
    ["False","False","False","True"],
    ])

#------------------------------------------------------------Motor Paso a Paso del Timón-------------------------------------------------------
class PaP():

    def __init__(self, pin1, pin2, pin3, pin4):

        self.pin1= pin1
        self.pin2= pin2
        self.pin3= pin3
        self.pin4= pin4

        #Defino los pines como salida
        gpio.setup(self.pin1, gpio.OUT)
        gpio.setup(self.pin2, gpio.OUT)
        gpio.setup(self.pin3, gpio.OUT)
        gpio.setup(self.pin4, gpio.OUT)
        
        gpio.output(self.pin1, 0)
        gpio.output(self.pin2, 0)
        gpio.output(self.pin3, 0)
        gpio.output(self.pin4, 0)
    
    #--------------------------------------------Giro horario---------------------------------------------------
    def girarH(self): #Funcion para girar el timón horario (Valores negativos del pote)
        for e in range (0,4):   #Activo todos los estados para ir girando el motor hasta lleagr al valor deseado
                    
            if estados[e, 0] == "True":
                gpio.output(self.pin1, 1)
            else:
                gpio.output(self.pin1, 0)

            if estados[e, 1] == "True":
                gpio.output(self.pin2, 1)
            else:
                gpio.output(self.pin2, 0)

            if estados[e, 2] == "True":
                gpio.output(self.pin3, 1)
            else:
                gpio.output(self.pin3, 0)
                    
            if estados[e, 3] == "True":
                gpio.output(self.pin4, 1)
            else:
                gpio.output(self.pin4, 0)
            
            time.sleep(0.003)

        self.detener()
        return 0

    #-------------------------------------------Giro antihorario--------------------------------------------
    def girarAH(self): #Funcion para girar el timón antihorario (Valores positivos del pote)
        for e in range (0,4):

            if estados[e, 3] == "True":
                gpio.output(self.pin1, 1)
            else:
                gpio.output(self.pin1, 0)

            if estados[e, 2] == "True":
                gpio.output(self.pin2, 1)
            else:
                gpio.output(self.pin2, 0)

            if estados[e, 1] == "True":
                gpio.output(self.pin3, 1)
            else:
                gpio.output(self.pin3, 0)
                    
            if estados[e, 0] == "True":
                gpio.output(self.pin4, 1)
            else:
                gpio.output(self.pin4, 0)
                
            time.sleep(0.003)

        self.detener()
        return 0
    #-------------------------------------------Función Detener--------------------------------------------
    def detener(self):

        gpio.output(self.pin1, 0)
        gpio.output(self.pin2, 0)
        gpio.output(self.pin3, 0)
        gpio.output(self.pin4, 0)
        
        return 0
#----------------------------------------------------------------------------------------------------------------------------------------------

#---------------------------------------------------------Motor de la Cinta Transportadora-----------------------------------------------------
class Cangilon():
#El puente H que controla este motor funciona con un Multiplexor en la entrada para direccionar la señal PWM en ambos sentidos de giro.
#Esto es debido a que la Raspberry no cuenta con suficientes pines PWM. Entonces de esta forma utilizamos solo un pin PWM y una output normal.
    def __init__(self, pin1, pin2, pwm):

        self.pin1= pin1 #Pin de selección de sentido de giro
        self.pin2= pin2 #Pin PWM
        self.pwm= pwm   #porcentaje de encendido del pwm

        #Defino el pin como PWM
        gpio.setup(self.pin2, gpio.OUT)
        self.PWM= gpio.PWM(self.pin2, pwm)

    #---------------------------------------------Función de giro Horario-----------------------------------------------
    def girarD(self):
        self.PWM.stop()     #Paro el PWM
        gpio.output(self.pin1, 1)       #Cambio el sentido de giro. Con el pin en TRUE el giro es horario
        self.PWM.start(self.pwm)        #Inicio nuevamente el PWM

        return 0
    #--------------------------------------------Función de giro antiHorario--------------------------------------------
    def girarI(self):
        self.PWM.stop()     #Paro el PWM
        gpio.output(self.pin1, 0)       #Cambio el sentido de giro. Con el pin en FALSE el giro es antihorario
        self.PWM.start(self.pwm)        #Inicio nuevamente el PWM

        return 0

    #------------------------------------------------Función de Detener-------------------------------------------------
    def detener(self):
        #En esta función simplemente pongo todo en 0
        self.PWM.stop()
        gpio.output(self.pin1, 0)
        
        return 0
#----------------------------------------------------------------------------------------------------------------------------------------------

#----------------------------------------------------------------Motor de Propulsión-----------------------------------------------------------
class Propulsion():

    def __init__(self, pin1, pin2, pwm):

        #Inicio los pines y los defino como PWM
        self.pin1= pin1
        self.pin2= pin2
        self.pwm= pwm

        #Configuro los pines como PWM
        gpio.setup(self.pin1, gpio.OUT)
        gpio.setup(self.pin2, gpio.OUT)

        self.PWM1= gpio.PWM(self.pin1, pwm)
        self.PWM2= gpio.PWM(self.pin2, pwm)

        self.PWM1.stop()
        self.PWM2.stop()

    #---------------------------------------------Función de giro Horario-----------------------------------------------
    def girarD(self):   #Giro horario
        self.PWM1.stop()    #Paro uno de los pines
        self.PWM2.start(self.pwm)   #Enciendo el otro

        return 0

    #--------------------------------------------Función de giro antiHorario--------------------------------------------
    def girarI(self):   #Giro antihorario
        self.PWM2.stop()    #Paro uno de los pines
        self.PWM1.start(self.pwm)   #Enciendo el otro

        return 0

    #------------------------------------------------Función de Detener-------------------------------------------------
    def detener(self):
        #En esta función simplemente detenemos ambos
        self.PWM1.stop()
        self.PWM2.stop()
        
        return 0

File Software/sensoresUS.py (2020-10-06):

#Esta es la librería que utilizamos para controlar las mediciones de los sensores Ultrasónicos
import time
import RPi.GPIO as GPIO
import numpy as np 

#--------------------Configuración de los Pines-----------------------
TRIG1 = 5
TRIG2 = 2 
ECHO = 26 

GPIO.setmode(GPIO.BCM)
# Establecer que TRIG es un canal de salida.
GPIO.setup(TRIG1, GPIO.OUT)
GPIO.setup(TRIG2, GPIO.OUT)
# Establecer que ECHO es un canal de entrada.
GPIO.setup(ECHO, GPIO.IN)

#Pines de control de los multiplexores
GPIO.setup(23, GPIO.OUT)
GPIO.setup(24, GPIO.OUT)
GPIO.setup(25, GPIO.OUT)

#hay que darle unos segundos a los sensores para que se estabilicen
GPIO.output(TRIG1, 0)
GPIO.output(TRIG2, 1)
time.sleep(2)
#---------------------------------------------------------------------

def medicion():	#Esta es la función que realiza la medición con los sensores

	# Prender el pin activador por 10 microsegundos
	# y después volverlo a apagar.
	GPIO.output(TRIG1, 1)
	GPIO.output(TRIG2, 0)
	time.sleep(0.00001)
	GPIO.output(TRIG1, 0)
	GPIO.output(TRIG2, 1)
	# En este momento el sensor envía 8 pulsos
	# y pone a ECHO en HIGH
	# cuando llegan los pulsos lo pone en LOW
	# hay que medir el tiempo 

	while True:	
		if (GPIO.input(ECHO) == 1):
			break

	pulso_inicio = time.time()
	while True:
		if (GPIO.input(ECHO) == 0):
			break
	pulso_fin = time.time()

	# La medición del tiempo es en segundos.
	duracion = pulso_fin - pulso_inicio

	# Calcular la distancia usando la velocidad del
	# sonido y considerando que la duración incluye
	# la ida y vuelta.
	distancia = (17150 * duracion)

	return distancia

def lectura():	#Esta función va variando los pines selectores de los multiplexores para medir de forma sincrónica
#con los 8 sensores. Además los guarda en un array para mayor facilidad.

	datos= np.empty((1, 8))	#Array que guarda los datos de distancia de los sensores
	pos=0	#Numero que se va sumando para ir pasando de sensor en sensor
	#Realizamos varios bucles para poder llamar a todos los ultrasónicos con los pines selectores
	for i in (0, 1):
		for j in (0, 1):
			for k in (0, 1):
				GPIO.output(23, i)
				GPIO.output(24, j)
				GPIO.output(25, k)
				datos[0, pos]= medicion()
				
				if (datos[pos] > 400):	#Acá indicamos que si el sensor no mide nada (mayor a 400m) indique un 0
					datos[pos]=0

				pos+=1
	return datos
			

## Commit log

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2020-05-06 se agrego mensaje de bienvenida y se conecto el resultado con su funcion
2020-05-06 Update main.py
    Correxión de parentesis en el print y faltaba agregar el resulatado en la funcion de muestraDeResultado
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2020-05-11 Archivo de proteus
    Cree un archivo de proteus para los modulos de RF
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2020-05-12 Carpeta de Diseño
    [BARQUIDOU SIN FLOTADOR 1.3dm, BARQUIDOU SIN FLOTADOR 1.obj, BARQUIDOU SIN FLOTADOR obj 111.obj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]
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2020-05-12 Carpeta de Hardware
    [Circuito de Control de Marcha.kicad_pcb, Circuito de Control de Marcha.sch, Lista de Componentes.xlsx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]
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2020-05-14 Regulador de carga
    Modifique el circuito regulador de carga para hacerlo mas compacto y con menor consumo.
    [Regulador de Carga.sch]
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2020-05-14 Agregar huellas faltantes
    le agregue las huellas que faltaban al regulador de carga
    [Regulador de Carga.sch]
2020-05-15 regulador de carga (yeti)
    es mi primer placa despues de años. ¿esta fachera, no?
    [Regulador de Carga.kicad_pcb, Regulador de Carga.sch]
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2020-05-19 Subir archivos de blender
    [Simple_Kayak.stl, animacion de la cinta transportadora.blend]
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2020-05-19 Animacion blender
    Cree la animacion de blender hay que achicar todo y cambiar los colores para poder renderzarlo
    [animacion de la cinta transportadora.blend]
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2020-05-20 Render animacion
    [animacion de la cinta transportadora.blend]
2020-05-20 Animacion
    Primera animacion completa, faltan realizar algunos cambios menores
    [animacion de la cinta transportadora.blend]
2020-05-20 Detalles finales de la animacion
    [animacion de la cinta transportadora.blend]
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2020-05-21 Borrar todos los modelos 3D al pedo
    [BARQUIDOU SIN FLOTADOR 1.3dm, BARQUIDOU SIN FLOTADOR 1.obj, BARQUIDOU SIN FLOTADOR obj 111.obj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]
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2020-05-26 Agregar animación
    [Simple_Kayak.stl, animacion de la cinta transportadora.blend]
2020-05-26 Update Lista de Componentes.xlsx
    [Lista de Componentes.xlsx]
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2020-05-27 Esquematico Regulador de Carga
    Agregue los 4 diodos en el esquematico.
    [Regulador de Carga.sch]
2020-05-27 PCB regulador de carga
    [Regulador de Carga.kicad_pcb]
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2020-06-02 Eliminar archivos que estan de mas
    [Cangilon (michy).obj, Tacho(Michy).obj, barco2 arreglado x3 (michy) (2).obj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]
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2020-06-07 Actualizar el regulador de carga
    Cambie los tres diodos y el transistor por un operacional en modo comparador.
    [Regulador de Carga.sch]
2020-06-07 Actualice el PCB del regulador de carga
    [Regulador de Carga.kicad_pcb]
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2020-06-07 Corregir errores del RC
    [Regulador de Carga.kicad_pcb, Regulador de Carga.sch]
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2020-06-08 SensoresUS
    Placa para control de sensores US con multiplexores
    [SensoresUS.kicad_pcb, SensoresUS.sch]
2020-06-08 Placa SUS
    Cambio de integrados
    [SensoresUS.kicad_pcb, SensoresUS.sch]
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2020-06-11 Actualizar el esquemático
    [Regulador de Carga.sch]
2020-06-11 Actualizar el PCB
    [Regulador de Carga.kicad_pcb]
2020-06-11 Detalles del PCB
    [Regulador de Carga.kicad_pcb]
2020-06-11 Sacar captura para trello
    [Regulador de Carga.sch]
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2020-06-25 Esquematico sensores de corriente
    Hice el circuito esquematico de los sensores de corriente con el conversor a/d.
    [Sensores analógicos.kicad_pcb, Sensores analógicos.sch]
2020-06-25 PCB de los sensores de corriente
    [Sensores analógicos.kicad_pcb, Sensores analógicos.sch]
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2020-06-25 Servidor Socket Qt
    Aca subo el programa del servidor del qt, el cliente tiene algunos errores asi que lo subo en un rato
2020-06-27 Esquematico sensor porcentaje de bateria
    [Sensores analógicos.sch]
2020-06-27 PCB Sensor de porcentaje de bateria
    [Sensores analógicos.kicad_pcb, Sensores analógicos.sch]
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2020-06-29 Actualizacion de placas
    [Regulador de Carga.kicad_pcb, Regulador de Carga.sch, Sensores analógicos.kicad_pcb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]
2020-06-29 Correxion en el control de marcha
    [Circuito de Control de Marcha.kicad_pcb, Circuito de Control de Marcha.sch]
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2020-07-02 Preparar para impresion
    Prepare todas las placas para imprimirlas
    [Circuito de Control de Marcha.kicad_pcb, Regulador de Carga.kicad_pcb, Regulador de Carga.sch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]
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2020-07-04 Esquematico CCM
    Puse los optoacopladores en el controlador de marcha
    [Circuito de Control de Marcha.sch]
2020-07-04 PCB control de marcha
    Intente hacer el PCB pero me queda una conexion de los púentes H
    [Circuito de Control de Marcha.kicad_pcb, Circuito de Control de Marcha.sch]
2020-07-04 Circuito de Control de Marcha
    Correccion de PCB
    [Circuito de Control de Marcha opto final.kicad_pcb, Circuito de Control de Marcha.sch]
2020-07-06 Update and rename deteccion-py.py to deteccion.py
    le arregle el nombre
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2020-07-07 Agregar USB y errores de impresion
    Agregue un conector USB al regulador de 5V y corregí los errores de impresión
2020-07-07 CCM
    agregue un mux en el puente del cangilon para controlarlo con un solo pwm
    [Circuito de Control de Marcha opto final.kicad_pcb, Circuito de Control de Marcha.sch]
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2020-07-07 lista de componentes
    [Lista de Componentes.xlsx]
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2020-07-08 Ultimos detalles CCM
    Achique un poco la placa y la prepare para imprimir
    [Circuito de Control de Marcha opto final.kicad_pcb]
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2020-07-16 Conversor A/D
    le agruegue as pines de conexion al conversor
    [Sensores analógicos.kicad_pcb]
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2020-08-10 Update RedNeuronal.py
    arreglos en el codigo, agregue la nueva funcion de salida
    [RedNeuronal.py]
2020-08-11 Update Primeras_pruebas_M_dulo_Master.ino
    Compile el programa y cambie errores de sintaxis
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2020-08-24 CorreccionGPIO
    mismo problema que en los motores
    [sensoresUS.py]
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2020-09-05 ADC
    arreglo en el codigo de SPI
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2020-09-06 Arreglar algunas cosas de la presentacion en ingles
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2020-09-22 simulacion
    arreglo de dos bugs
    [Barco.pde, Colision.pde, Sim.pde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]
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2020-09-23 Revert "Merge branch 'develop' of https://github.com/impatrq/ecoboat into develop"
    This reverts commit c2cc32374c72a0522cc8cb1eb312718b49fe36d2, reversing
    changes made to 7f76536615141b28521b4e4c5f1dff92085f24e4.
    [Barco.pde, Sim.pde]
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2020-10-02 Update Carpeta Técnica EcoBoat.docx
    Corregir errores de ortografia y agregue los DNIs de todos
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2020-10-07 Retoques a la carpeta tecninca
    Arregle las tabulaciones de la parte de software y complete el inicio
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2020-10-13 Carpeta tecnica
    Arregle las tabulaciones del anexo. Agregue un par de cosas en estructura y empece a poner la bibliografia
2020-10-14 Emprolijar el repositorio
    [Base.obj, Circuito de Control de Marcha.kicad_pcb, Depósito de Basura.obj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]
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
